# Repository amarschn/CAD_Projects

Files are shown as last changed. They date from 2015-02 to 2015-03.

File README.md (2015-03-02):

# CAD_Projects

MRSD Project:
=============

In this project my team and I (4 members) are focused on creating a modular robotic platform. Modules have been broken out based on different functions, such as perception, locomotion, and brain. We use ROS for inter-module communication over ethernet.

For this modular platform we built a mobile robot for the first semester consisting of a perception module, locomotion module, and brain module. The perception module was a pan/tilt Kinect camera which could be used for line sensing and tele-operation. The locomotion module was a differential drive system using 2 DC motors and caster wheels for support. The brain module was an Intel-i3 computer running ROS and controlling all other modules, a 24V battery, and voltage converter.

More details can be found at:
https://sites.google.com/site/mrsdproject201415teamd/

Semester 1:
-----------

Below is a picture of the full assembly of the last semester's robot.
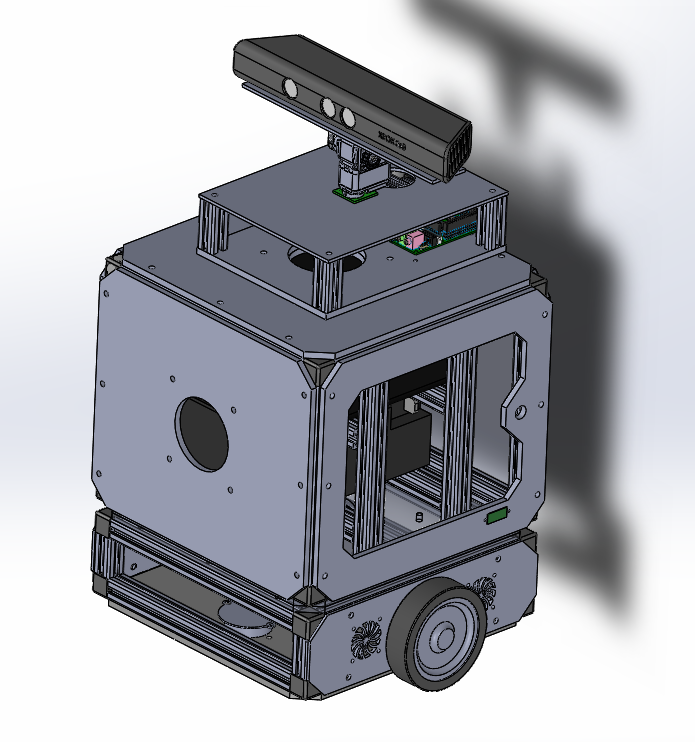
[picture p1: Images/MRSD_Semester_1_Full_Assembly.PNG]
Robot Assembly


The design of this robot was rather rushed, and so I focused on minimal build time and easy access to internal components (which proved smart, as the team and I had to dis-assemble and re-assemble the robot many times during testing in order to get access to electronic components). This was my first heavy use of Solidworks, as at Qualcomm I used Pro-Engineer/Creo. Overall I found the 2 programs more similar than different so the learning curve was not too bad.

At Qualcomm I used a top-down design method when constructing assemblies, which has it's pros and cons, but this time around I tried a different tack. I used a text file ("globals.txt") that contained global variables such as module height, width, etc.. I then imported the "global" variables into given Solidworks parts to access the variables I needed. This allowed me to quickly tweak robot physical parameters and have the changes affect all parts at once.

Here is the actual robot once constructed:
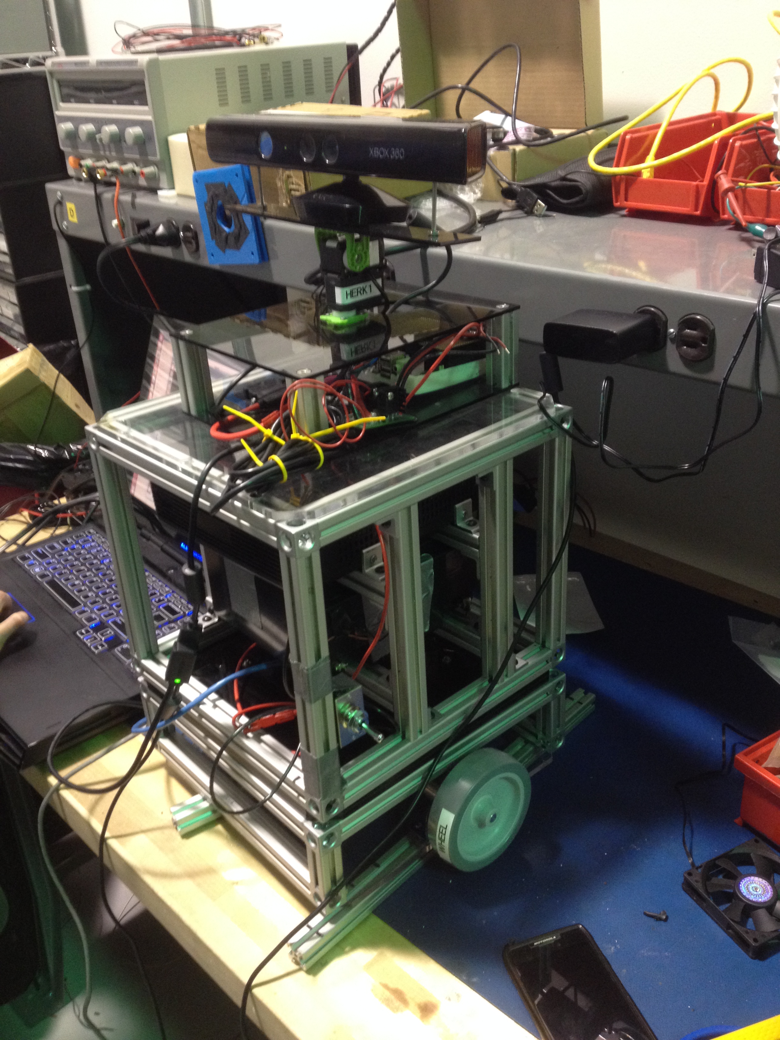
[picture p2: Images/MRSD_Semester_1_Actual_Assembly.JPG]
Actual Robot Assembly


This was my first mobile robot design, and I learned a lot from it. The large unfilled holes you see are for an inter-module connector. We were not able to finish a satisfactory inter-module connector in time for the end of last semester, and so the holes were used for ethernet and power wires.

I used laser-cut acrylic and aluminum extrusion as the mechanical structure of the robot. Due to time constraints I wanted something that was cheap, durable, and cost very little machining time. I had access to Makerbot 3D printers, which while useful for small parts are not useful for large, detailed, or load-bearing components.

Once all modules were assembled, the motor power was not always enough to get the robot moving over the rough pavement we demo'd on. The wear and tear of driving on rough pavement eventually caused a gear tooth in one of the motors' gearheads to crack (right before a demo of course), forcing us to change out the locomotion module for an existing mobile base for the final demo.

Semester 2 (now):
-----------------

This semester I have gone back to basics. I am re-designing the robot from the ground up, first focusing on the inter-module connection, as it is in many ways the most unique aspect of the robot. I came up with many different design possibilities, but eventually settled on a magnetic inter-module connector. Magnets offer many advantages, as the connection mechanical strength can be scaled to a point with larger magnets, and the disengagement between modules is linear. By this I mean that no special actions are required by the user to disengage a module other than pulling it. Additionally, by placing the magnets in certain pole orientations you can prevent the user from connecting 2 modules in an incorrect way.

This [paper](http://cba.mit.edu/docs/theses/10.06.knaian.pdf) considers many of the connector types I toyed with before settling on magnets. Ideally I would be able to prototype more of them, but there is not enough time before the end of the semester to fully explore all connector possibilities.

For the electrical connection I am using pogo pins, which are used to transmit power and data over 16 pins. I have used pogo pins before, and I think they are a no-brainer for applications such as this.

I am also using dowel pins as guide rods, which ensure an accurate pogo connection.

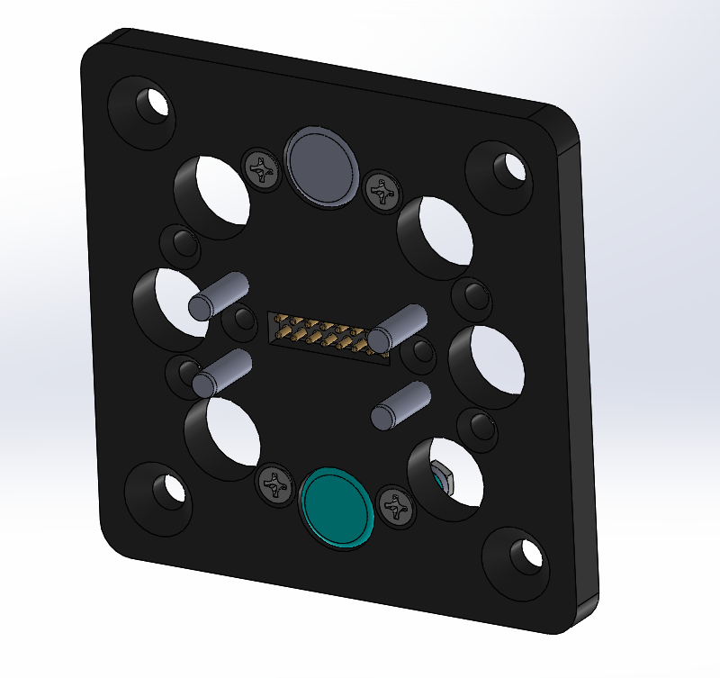
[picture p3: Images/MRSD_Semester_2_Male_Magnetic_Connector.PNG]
Male Magnetic Connector


This is the male connector, which as you can see is not using all of the magnet placement holes. This is because there was not enough room in the motor module for mounting all of them (the aluminum extrusion supports got in the way). This design is in a state of change however, and I am planning on using a different magnet placement grid to allow for more magnets.

The first module we have tested this magnetic connector with is a "motor module". This is a new module, one step lower than a locomotion module. The plan is to have motor modules that can be swapped out of a locomotion module, these different motor modules can have different kinds of motors as well as different wheel attachments. Once connected each motor module will communicate these details to the brain, which will dynamically update the robot's model. Below you can see the current CAD model for the motor module.

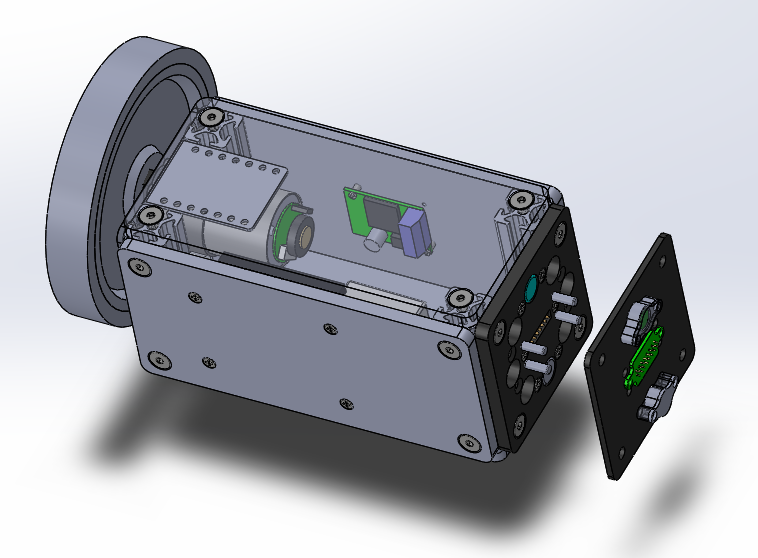
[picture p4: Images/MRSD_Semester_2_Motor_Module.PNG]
Motor Module


We have now built 2 of these, and they work pretty well! The magnetic connector works and is relatively sturdy. The next steps are to rebuild a locomotion base which will accept motor modules of this size, and to add the magnetic connector to appropriate faces of the brain module. We also will be building sensor modules using the same form factor as the motor module. So say the locomotion module had 4 different module connectors, you could swap out different motors and sensors quickly and easily and have an entirely new kind of robot! I am pretty excited about it and think by the end of the semester we will have a very cool re-configurable robot.

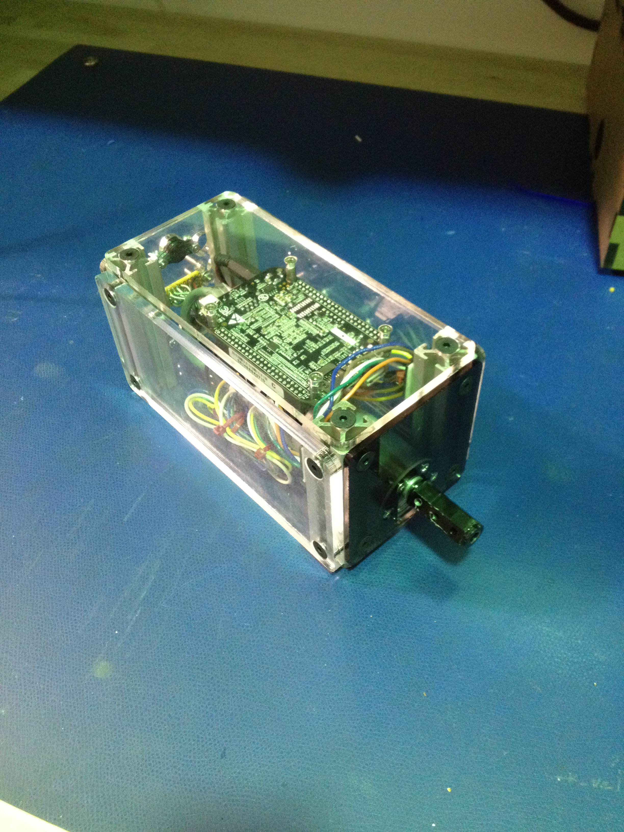
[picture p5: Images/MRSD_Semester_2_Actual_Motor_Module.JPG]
Actual Motor Module

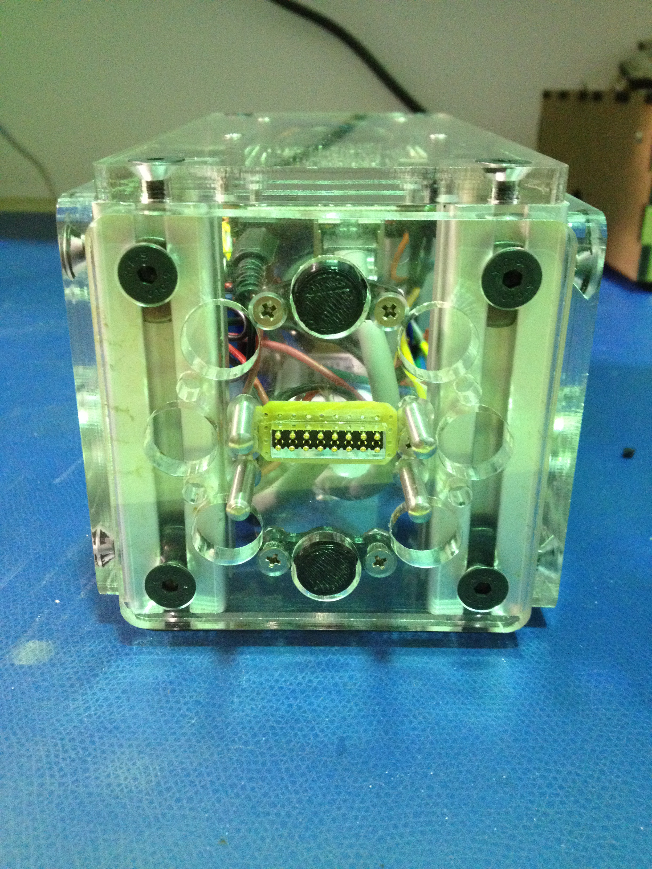
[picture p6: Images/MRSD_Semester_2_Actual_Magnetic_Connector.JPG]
Motor Module Connector


For the locomotion module, the plan is to have 4 module slots open to motor or sensor modules with the same form factor as the motor module seen above. I am trying to create a more visually pleasing aesthetic as compared to last semester. Below is one of the concepts for the module:

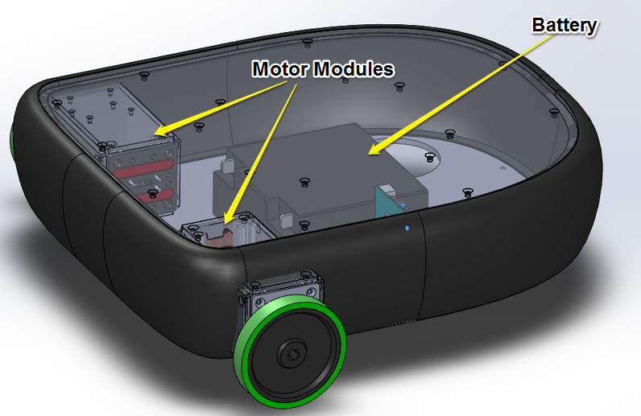
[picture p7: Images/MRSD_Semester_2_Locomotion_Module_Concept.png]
Locomotion Module Concept


By using laser cut acrylic or delrin on the top and bottom, and a thin 3D-printed ABS shell, the robot will be much more sleek as well as well within the team's limited budget.

Automated Durometer:
--------------------

The files for this project are located in a different repository, which can be found [here] (https://github.com/amarschn/Durometer_Assembly). The top-level assembly is called 'Durometer_Assembly' and can be downloaded in STP format if necessary.

This was a brief project I worked on over Christmas break. The goal was to automate a durometer (device for measuring hardness of different materials, in this case different kinds of rubber) for a scientific devices manufacturer.

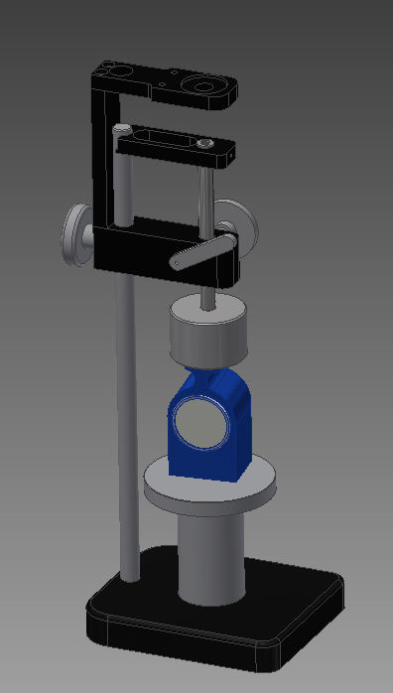
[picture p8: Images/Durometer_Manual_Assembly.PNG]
Basic Durometer


I did this project in Autodesk Inventor, as I wanted to try it out to see what all of the fuss was about. Once again, being a parametric CAD program it wasn't too different from Solidworks or Pro-E. The usual sketch/extrude/repeat process was mostly the same. My other focus was off-the-shelf material, as I did not have access to any kind of fabrication facilities during the majority of the break and so had to work with whatever I could get. McMaster was (once again) a godsend for this project.

In automating the durometer, I decided to implement a stepper-motor/lead screw system for raising and lowering the durometer. Steppers are relatively cheap and combined with lead screws allow for very accurate motion control, and no power draw during inactivity.

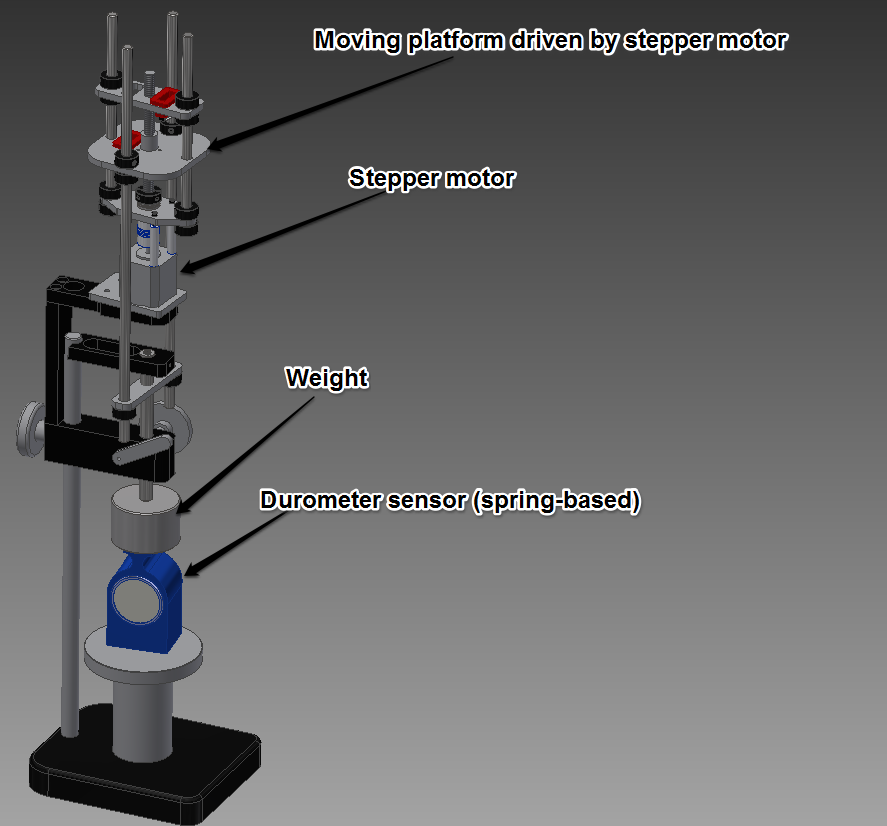
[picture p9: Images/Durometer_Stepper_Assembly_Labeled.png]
Automated Durometer

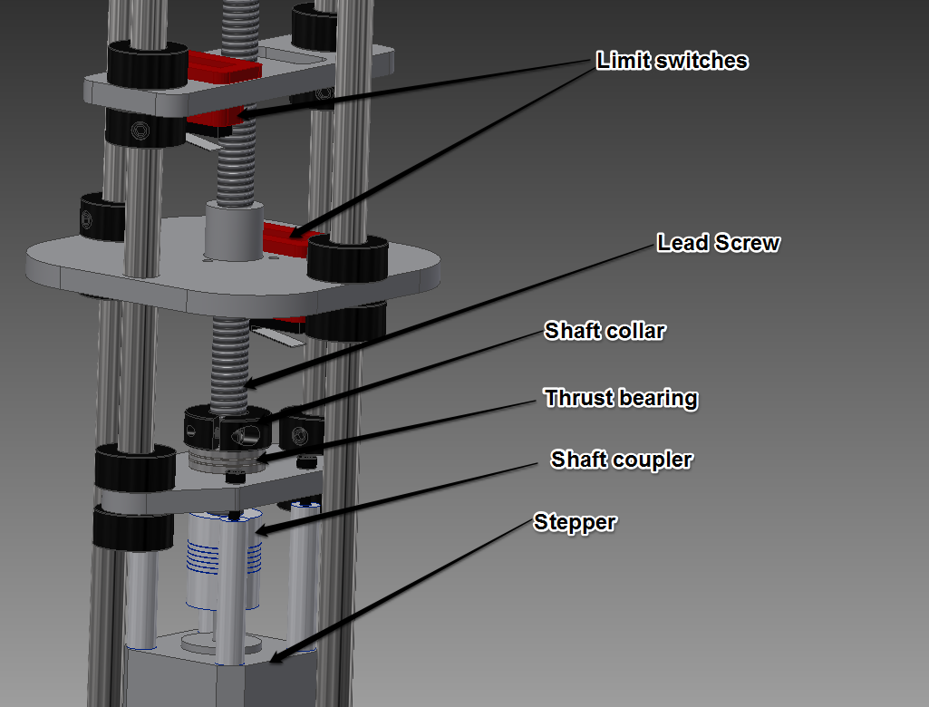
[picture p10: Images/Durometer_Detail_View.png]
Automated Durometer Detail


This project is currently on hiatus due to school taking up the majority of my time, but I was able to build a working prototype before the end of the break. Unfortunately I cannot find a video of it operating, but I will post that once I find it!

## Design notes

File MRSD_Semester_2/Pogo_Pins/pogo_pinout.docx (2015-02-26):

Female:

GND | GND | PWR | PWR | White w/orange stripe | White w/blue stripe | White w/green stripe | White w/brown stripe
GND | GND | PWR | PWR | Orange | Bue | Green | Brown

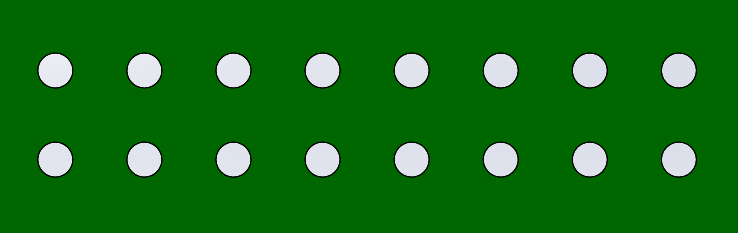
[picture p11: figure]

Male:

White w/brown stripe | White w/green stripe | White w/blue stripe | White w/orange stripe | PWR | PWR | GND | GND
Brown | Green | Blue | Orange | PWR | PWR | GND | GND

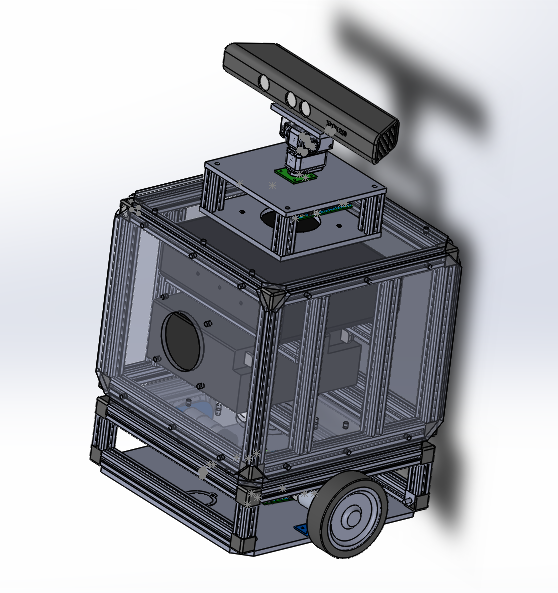
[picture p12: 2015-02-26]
MRSD_Semester_1/ILR4_img.png

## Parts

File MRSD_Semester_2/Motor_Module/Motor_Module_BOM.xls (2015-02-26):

ITEM NO. | PART NUMBER | DESCRIPTION | QTY.
1 | Motor |  | 1
2 | Motor Bracket |  | 1
3 | Motor Shaft Cover |  | 1
4 | Single Motor Driver |  | 1
5 | Rough BeagleBone Black |  | 1
6 | Motor_Module_Side_Pl ate |  | 1
7 | Motor_Module_Side_Pl ate |  | 1
8 | Motor_Module_Side_Pl ate |  | 1
9 | Motor_Module_Side_Pl ate |  | 1
10 | Motor_Module_Front_P late |  | 1
11 | Perm_Magnet_Male_Pl ate |  | 1
12 | 16pin_PCB |  | 1
13 | mill-max-823-22-016-10- 004101_P4XX-28-010- 00-090000 |  | 1
14 | mill-max-823-22-016-10- 004101_0963-0 |  | 16
15 | mill-max-823-22-016-10- 004101_0953-X |  | 16
16 | mill-max-823-22-016-10- 004101_0918-X |  | 16
17 | mill-max-823-22-016-10- 004101_6875-0-00-00- 75-XX-43-0C |  | 16
18 | Disc_Magnet_5862K65 |  | 8
19 | 93600A133 |  | 4
20 | T_Slot_Support |  | 4
21 | 91294A210 |  | 20
22 | 91771A059 |  | 2
23 | 94639A460 |  | 2
24 | 90730A001 |  | 2
25 | 91801A156 |  | 8
26 | 94868A164 |  | 4
27 | 90116A147 |  | 4
28 | Fastener_5537T454 |  | 16
29 | 91294A207 |  | 4
30 | 91801A154 |  | 6
31 | 90695A033 |  | 4
32 | Voltage Converter |  | 1

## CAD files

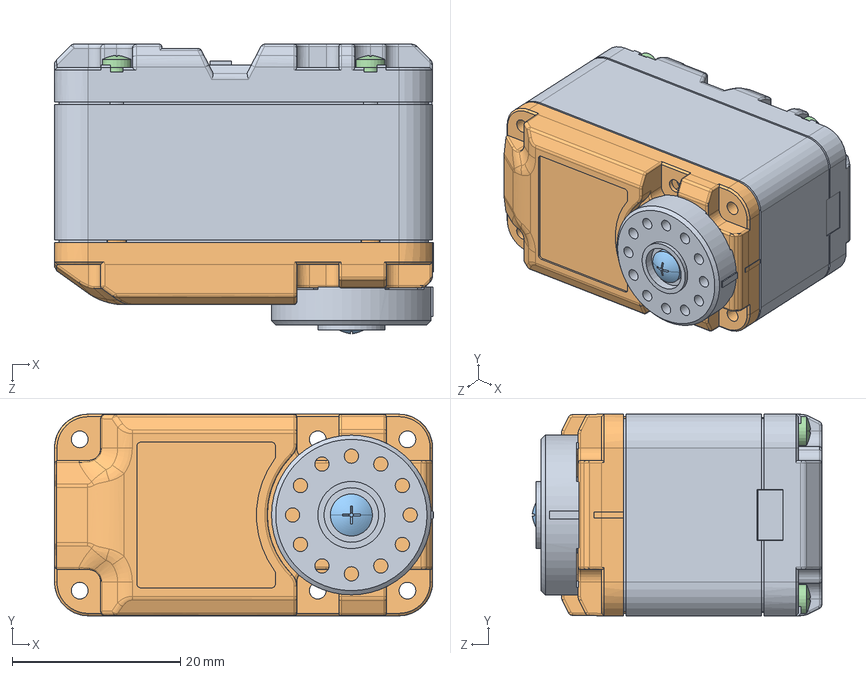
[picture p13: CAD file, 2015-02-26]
MRSD_Semester_1/SENSOR/herkulex.SLDASM
45.1 x 24.0 x 34.5 mm
Document
(#31287) TOP_191
(#129725) KSB1023A_M2_5X8Z
(#112458) KSB1023A_T2X25NI x 4

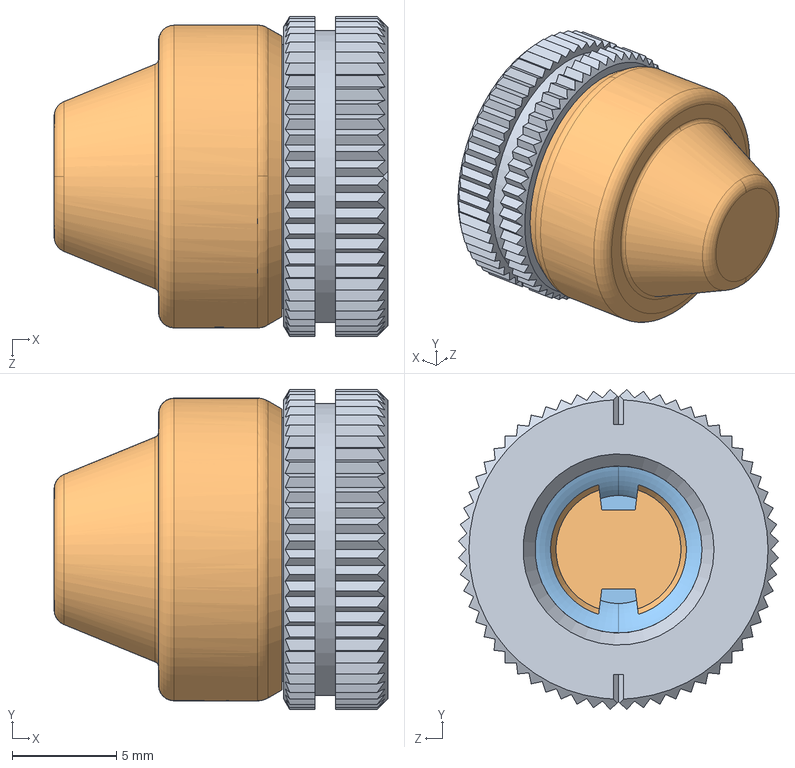
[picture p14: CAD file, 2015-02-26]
MRSD_Semester_2/Twist_Lock_Connectors/Southco-D8-336-100-300.SLDASM
16.0 x 15.3 x 15.3 mm
SW3dPS-D8-336-100-300_D8-336-101-300
SW3dPS-D8-336-100-300_D8-336-114-190-ASSY
SW3dPS-D8-336-100-300_D8-336-113-190

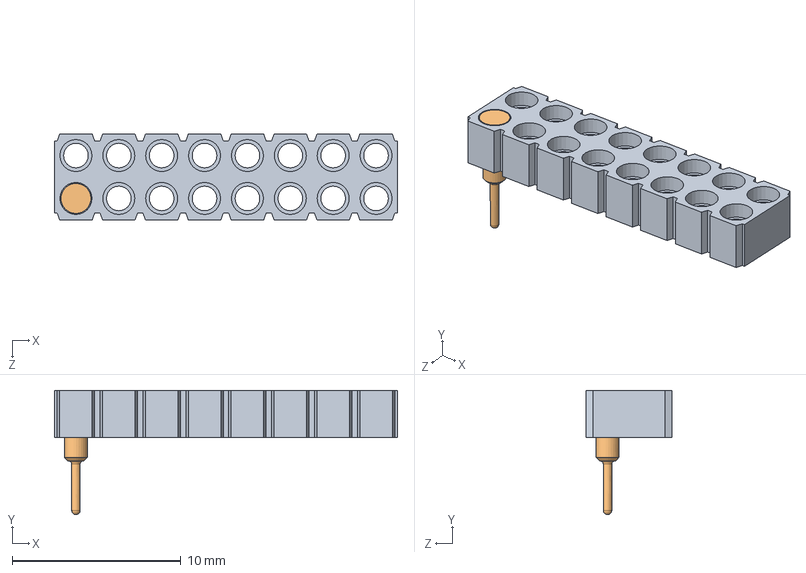
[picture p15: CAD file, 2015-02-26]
MRSD_Semester_2/Pogo_Pins/mill-max-419-10-216-00-001000/mill-max-419-10-216-00-001000.sldasm
20.3 x 7.37 x 5.08 mm
mill-max-419-10-216-00-001000_P4XX-21-010-00-000000
mill-max-419-10-216-00-001000_1942

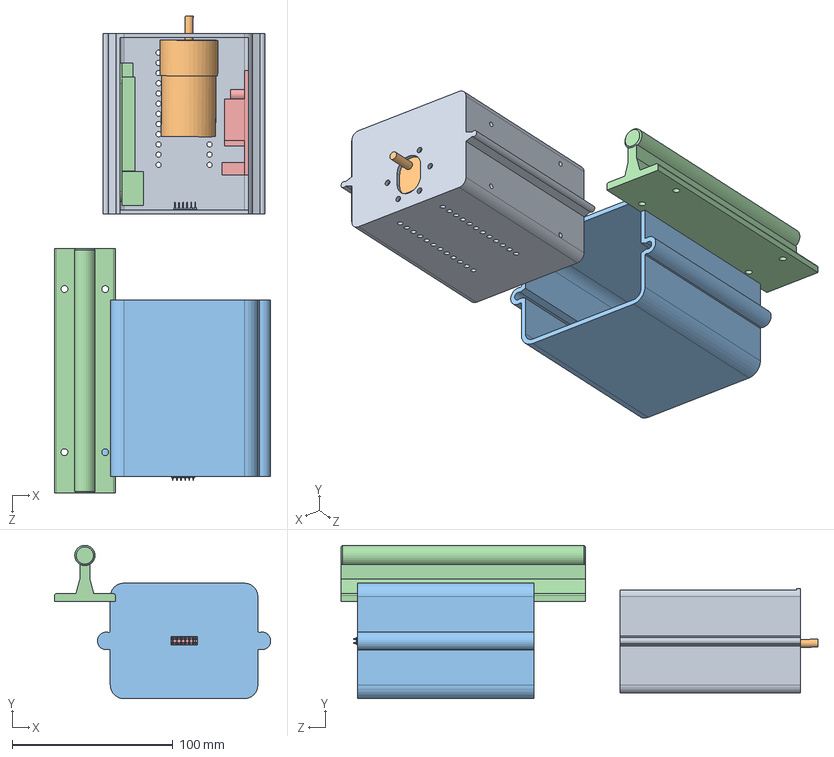
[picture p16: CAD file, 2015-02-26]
MRSD_Semester_2/Slide_Rail_Motor_Module/Slide_Rail_Assembly.SLDASM
134.8 x 95.5 x 297.1 mm
Slide_Rail_Motor_Housing
DC_Motor
Slide_Rail_Outer_Housing
Rough BeagleBone Black
mill-max-818-22-012-10-000101_P4XX-28-010-00-090000
mill-max-818-22-012-10-000101_0963-0 x 12
mill-max-818-22-012-10-000101_0954-0 x 12
mill-max-818-22-012-10-000101_0918-X x 12
mill-max-818-22-012-10-000101_6875-0-00-00-75-XX-43-0C x 12
mill-max-419-10-212-00-001000_P4XX-21-010-00-000000
mill-max-419-10-212-00-001000_1942 x 12
Slide_Rail_1049K110
Motor Driver

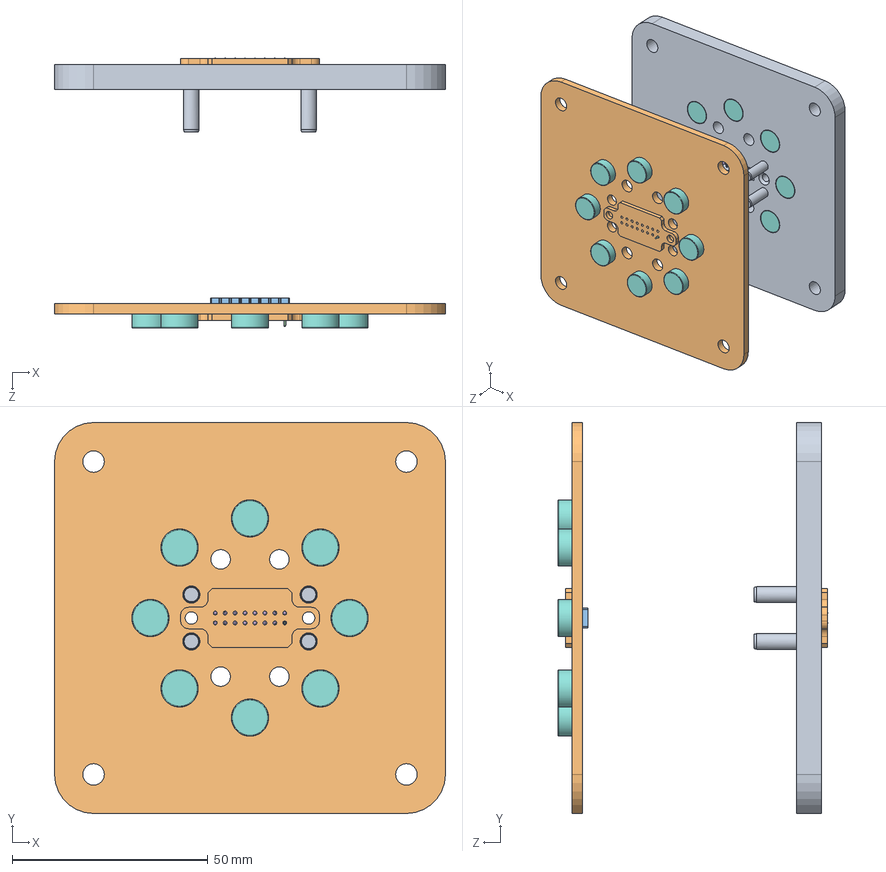
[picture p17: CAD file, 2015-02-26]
MRSD_Semester_2/Magnetic_Connectors/Perm_Magnet_Assembly.SLDASM
100.0 x 100.0 x 69.1 mm
Perm_Magnet_Male_Plate
16pin_PCB x 2
mill-max-823-22-016-10-004101_P4XX-28-010-00-090000
mill-max-823-22-016-10-004101_0963-0 x 16
mill-max-823-22-016-10-004101_0953-X x 16
mill-max-823-22-016-10-004101_0918-X x 16
mill-max-823-22-016-10-004101_6875-0-00-00-75-XX-43-0C x 16
Disc_Magnet_5862K65 x 16
Dowel_Pin_93600A133 x 4
Perm_Magnet_Female_Plate
mill-max-419-10-216-00-001000_P4XX-21-010-00-000000
mill-max-419-10-216-00-001000_1942

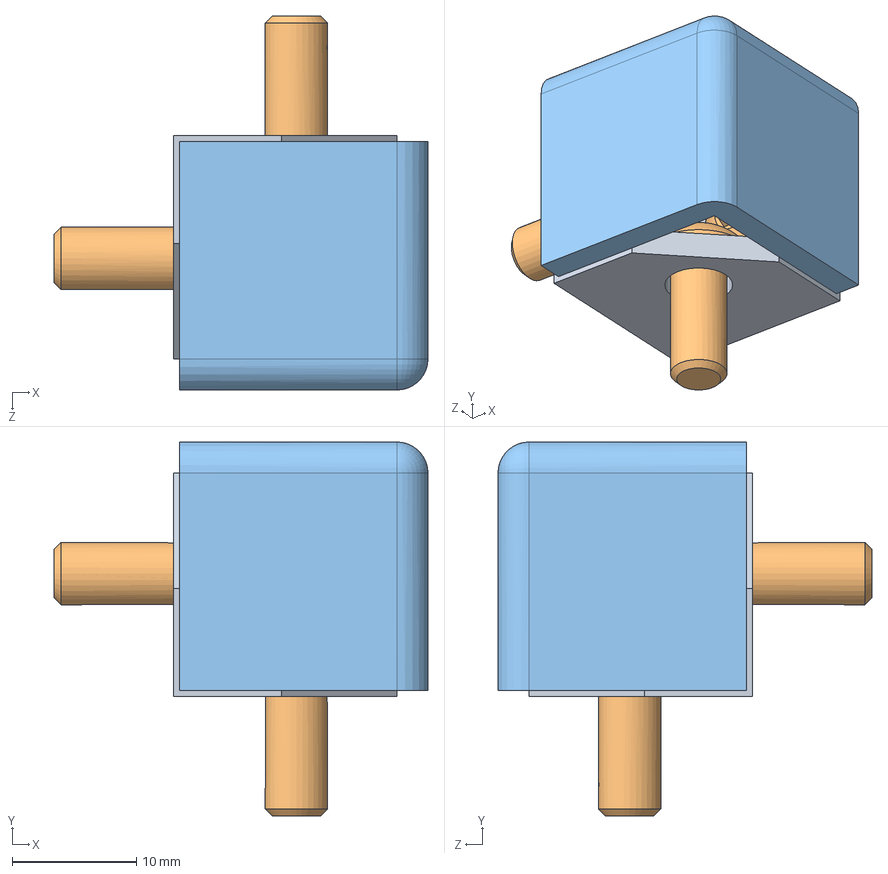
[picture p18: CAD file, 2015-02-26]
MRSD_Semester_1/BRAIN/corner_fastener.SLDASM
30.1 x 30.1 x 30.1 mm
corner_fastener_bracket
corner_fastener_screw x 3
corner_fastener_cover

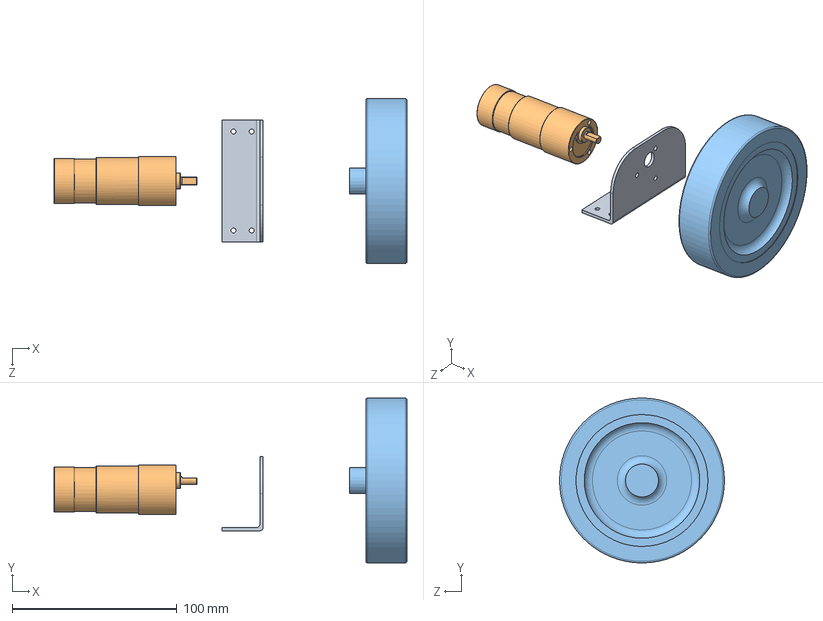
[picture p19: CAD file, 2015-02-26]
MRSD_Semester_1/LOCOMOTION/Devantech RD02 Drive System.SLDASM
214.1 x 99.9 x 100.0 mm
Devantech EMG30 Mounting Bracket
Devantech EMG30
Wheel

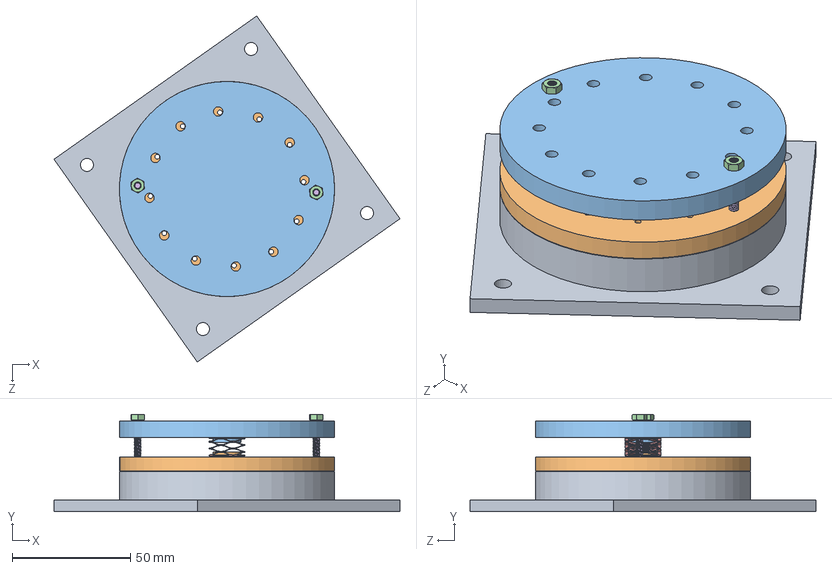
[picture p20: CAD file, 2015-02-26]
MRSD_Semester_1/CONNECTOR/bay con 12 mk2.SLDASM
146.3 x 41.1 x 146.3 mm
bayonet container 12
inner bayonet connector 12
bay container 12 bottom
m3 nut x 2
8mm length spring
M3 25MM x 2

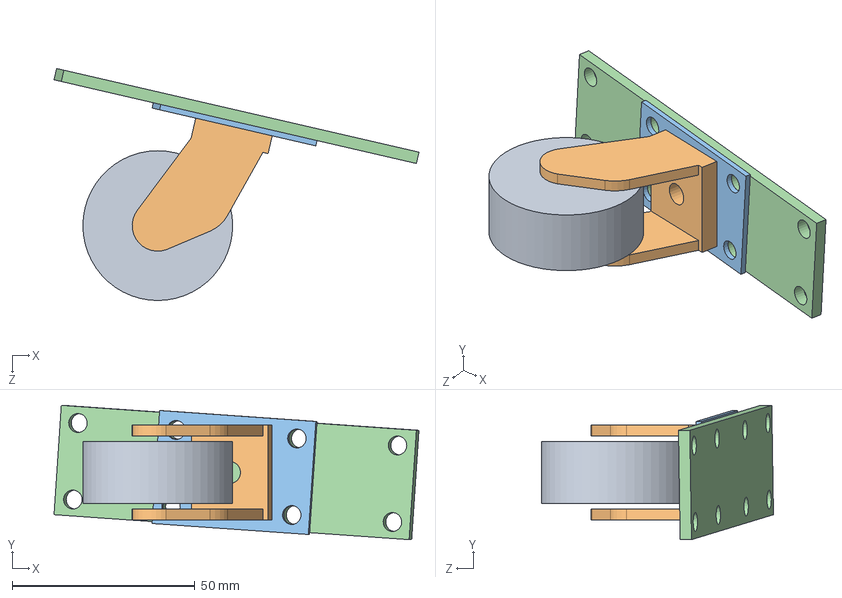
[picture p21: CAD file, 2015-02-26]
MRSD_Semester_1/LOCOMOTION/caster_wheel_assembly.SLDASM
99.9 x 36.8 x 63.5 mm
caster_wheel
caster_frame
caster_spin_plate
caster_mounting_plate

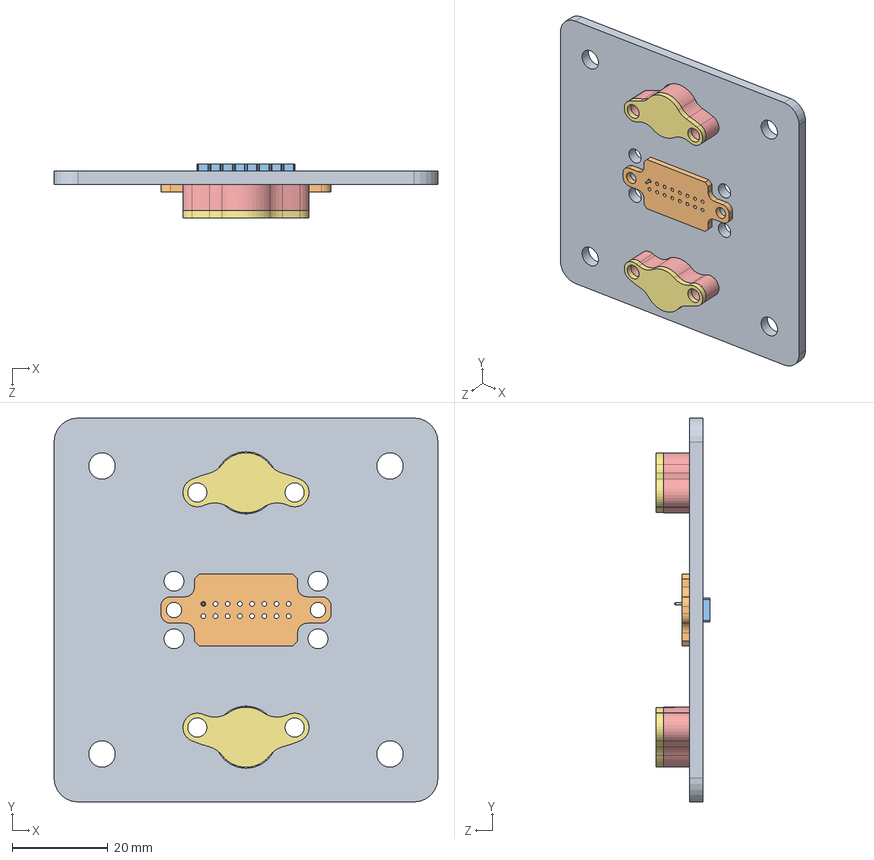
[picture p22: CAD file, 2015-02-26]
MRSD_Semester_2/Magnetic_Connectors/Female_Module_Connector_Assembly.SLDASM
80.0 x 80.0 x 11.2 mm
Perm_Magnet_Female_Plate
16pin_PCB
mill-max-419-10-216-00-001000_P4XX-21-010-00-000000
mill-max-419-10-216-00-001000_1942
Magnet_Containment_Vessel_Body x 2
Disc_Magnet_5862K65 x 2
Magnet_Containment_Vessel_Lid x 2

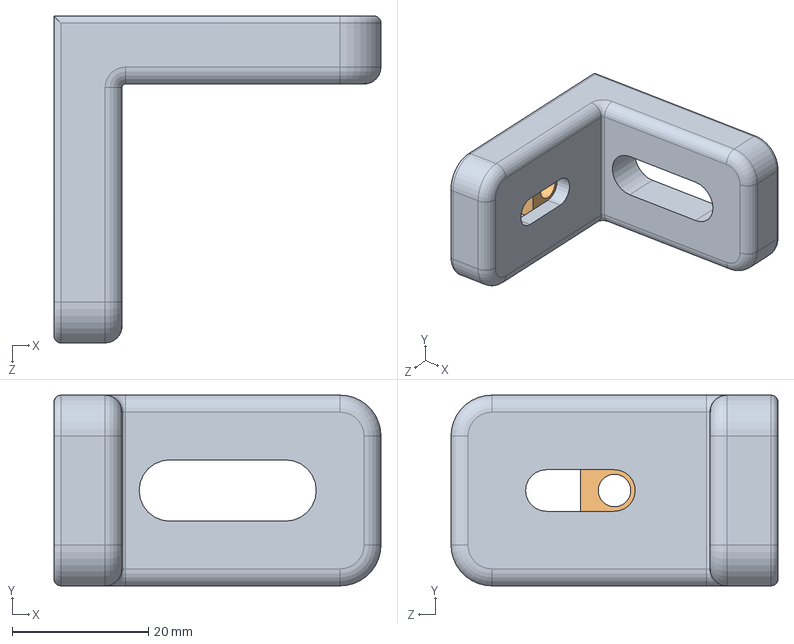
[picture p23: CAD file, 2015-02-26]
MRSD_Semester_1/BRAIN/t_slot_fastener.SLDASM
48.0 x 28.0 x 48.0 mm
t_slot_fastener_bracket
t_slot_fastener_slide

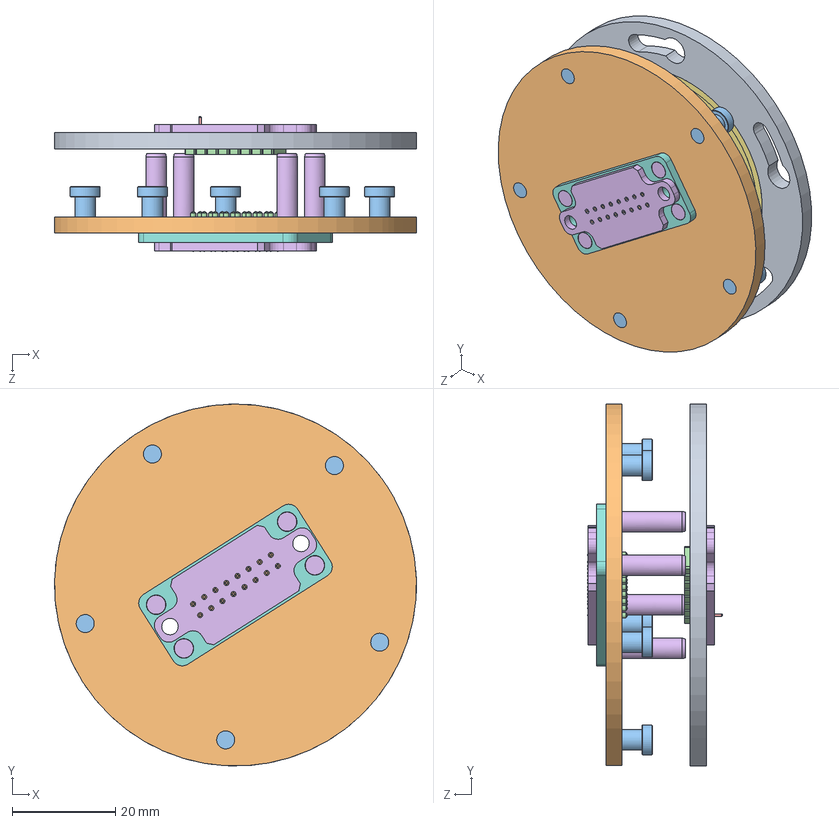
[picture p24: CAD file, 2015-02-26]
MRSD_Semester_2/Twist_Lock_Connectors/Star_Twist_Lock.SLDASM
70.0 x 70.0 x 26.2 mm
Star_Twist_Lock_Female_Plate
Star_Twist_Lock_Male_Plate
dowel_shelf_pin x 5
mill-max-419-10-216-00-001000_P4XX-21-010-00-000000
mill-max-419-10-216-00-001000_1942
Dowel_Pin_93600A133 x 4
Pogo_Fixture_Female_Front_Plate
Pogo_Fixture_Male_Front_Plate
mill-max-823-22-016-10-004101_P4XX-28-010-00-090000
mill-max-823-22-016-10-004101_0963-0 x 16
mill-max-823-22-016-10-004101_0953-X x 16
mill-max-823-22-016-10-004101_0918-X x 16
mill-max-823-22-016-10-004101_6875-0-00-00-75-XX-43-0C x 16
16pin_PCB x 2
Twist_Lock_Bearing

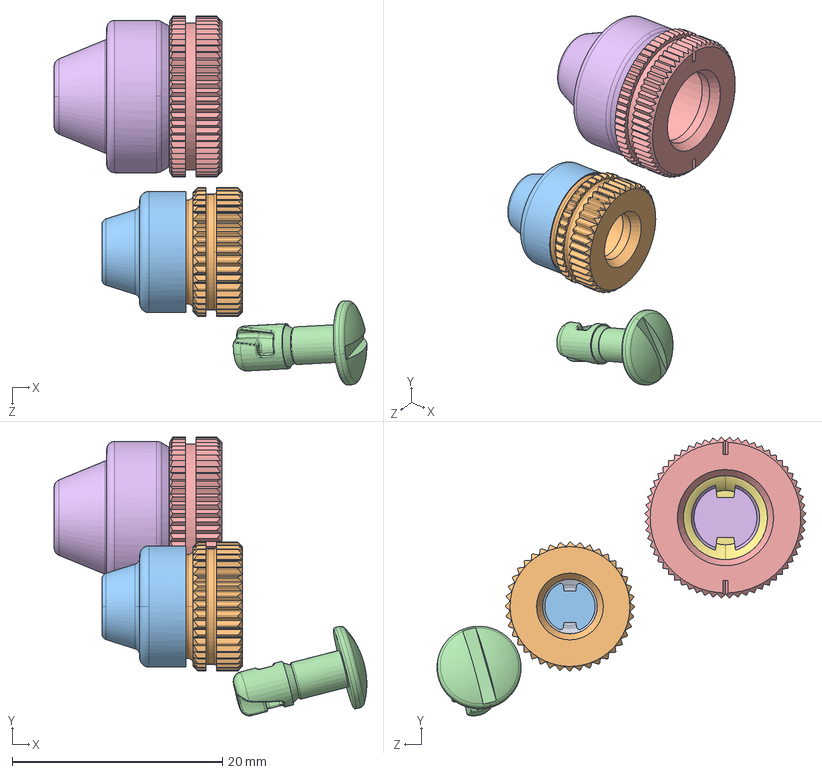
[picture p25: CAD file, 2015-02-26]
MRSD_Semester_2/Twist_Lock_Connectors/Test_Twist_Lock_Assembly.SLDASM
29.8 x 26.5 x 35.1 mm
SW3dPS-D8-334-100-300_TAB PLATE
SW3dPS-D8-334-100-300_D3_PANEX_Front_Mount_Insert_Body
SW3dPS-D8-334-100-300_D3_PANEX_Insert_Cup
Southco-D8-314-108-170
SW3dPS-D8-336-100-300_D8-336-101-300
SW3dPS-D8-336-100-300_D8-336-114-190-ASSY
SW3dPS-D8-336-100-300_D8-336-113-190

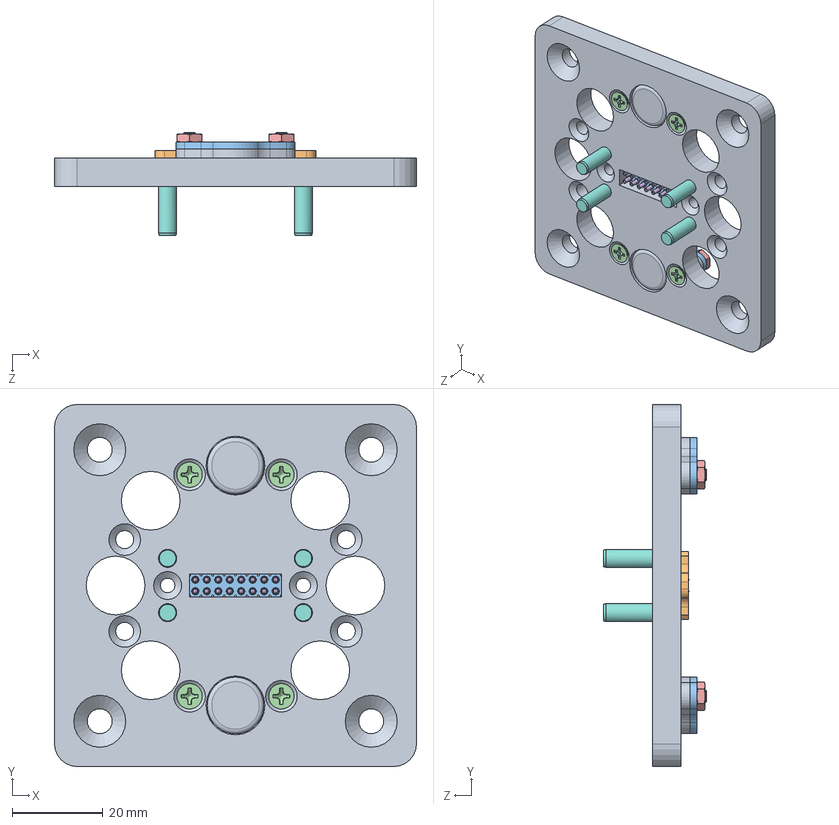
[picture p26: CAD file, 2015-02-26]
MRSD_Semester_2/Magnetic_Connectors/Male_Module_Connector_Assembly.SLDASM
80.0 x 80.0 x 22.9 mm
Perm_Magnet_Male_Plate
16pin_PCB
mill-max-823-22-016-10-004101_P4XX-28-010-00-090000
mill-max-823-22-016-10-004101_0963-0 x 16
mill-max-823-22-016-10-004101_0953-X x 16
mill-max-823-22-016-10-004101_0918-X x 16
mill-max-823-22-016-10-004101_6875-0-00-00-75-XX-43-0C x 16
Dowel_Pin_93600A133 x 4
Magnet_Containment_Vessel_Body x 2
Disc_Magnet_5862K65 x 2
Magnet_Containment_Vessel_Lid x 2
91801A158 x 4
90695A033 x 4

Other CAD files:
MRSD_Semester_2/Slide_Rail_Motor_Module/Locomotion_Base_Assembly.SLDASM
MRSD_Semester_2/Sketch_References/Perm_Magnet_Assembly_Reference.SLDPRT
MRSD_Semester_2/Magnetic_Connectors/Perm_Magnet_Assembly_Reference.SLDASM
MRSD_Semester_2/Pogo_Pins/16_pin_pogo_male_assembly.SLDASM
MRSD_Semester_1/ARM/gripper.stp
MRSD_Semester_1/ARM/uArm/gripper.stp
MRSD_Semester_1/BRAIN/5537T181.SLDPRT
MRSD_Semester_1/BRAIN/LED_voltage_display.SLDPRT
MRSD_Semester_1/BRAIN/anker_battery_form_factor.SLDPRT
MRSD_Semester_1/BRAIN/assembly_brain_1.SLDASM
MRSD_Semester_1/BRAIN/assembly_brain_1.SLDDRW
MRSD_Semester_1/BRAIN/brain_front_panel.DXF
MRSD_Semester_1/BRAIN/brain_front_panel.SLDPRT
MRSD_Semester_1/BRAIN/brain_side_panel.DXF
MRSD_Semester_1/BRAIN/brain_side_panel.SLDPRT
MRSD_Semester_1/BRAIN/brain_side_panel_vents.SLDPRT
MRSD_Semester_1/BRAIN/brain_top_panel.DXF
MRSD_Semester_1/BRAIN/brain_top_panel.SLDPRT
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

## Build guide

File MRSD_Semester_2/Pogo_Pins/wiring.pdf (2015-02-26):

Female:

GND | GND | PWR | PWR | White w/orange stripe | White w/green stripe | White w/blue stripe | White w/brown stripe
GND | GND | PWR | PWR | Orange | Bue | Green | Brown

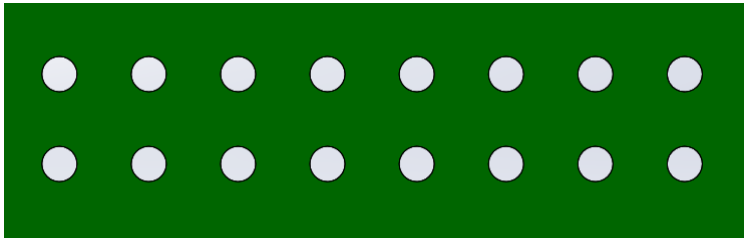
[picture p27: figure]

Male:

White w/brown stripe | White w/blue stripe | White w/green stripe | White w/orange stripe | PWR | PWR | GND | GND
Brown | Green | Bue | Orange | PWR | PWR | GND | GND

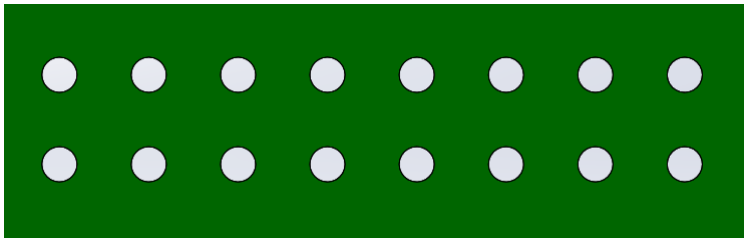
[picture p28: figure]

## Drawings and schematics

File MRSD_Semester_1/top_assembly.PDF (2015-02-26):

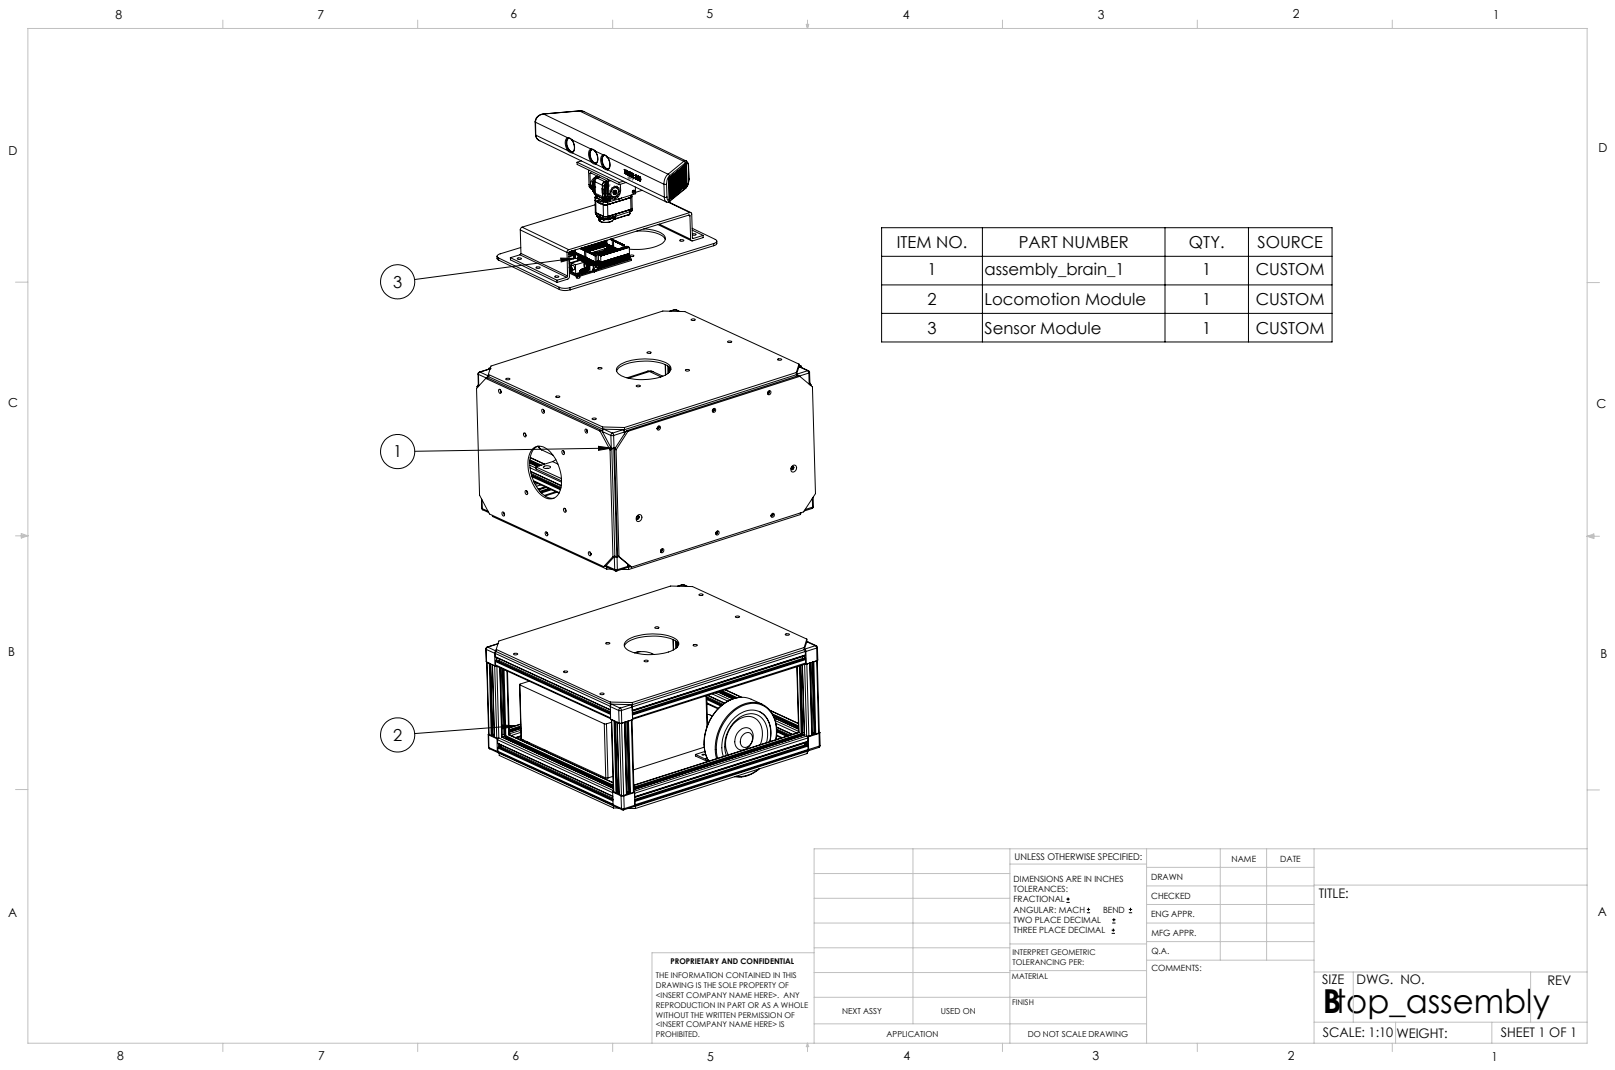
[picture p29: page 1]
NEXT ASSY; USED ON; ANGULAR: MACH; BEND; INTERPRET GEOMETRIC TOLERANCING PER:; ENG APPR.; MFG APPR.; DWG. NO.; REV; SCALE: 1:10 WEIGHT:; SHEET 1 OF 1

ITEM NO. | PART NUMBER | QTY. | SOURCE
1 | assembly_brain_1 | 1 | CUSTOM
2 | Locomotion Module | 1 | CUSTOM
3 | Sensor Module | 1 | CUSTOM

UNLESS OTHERWISE SPECIFIED:

DIMENSIONS ARE IN INCHES
TOLERANCES:
FRACTIONAL
TWO PLACE DECIMAL
THREE PLACE DECIMAL

PROPRIETARY AND CONFIDENTIAL
THE INFORMATION CONTAINED IN THIS
DRAWING IS THE SOLE PROPERTY OF
<INSERT COMPANY NAME HERE>. ANY
REPRODUCTION IN PART OR AS A WHOLE
WITHOUT THE WRITTEN PERMISSION OF
<INSERT COMPANY NAME HERE> IS
PROHIBITED.

DO NOT SCALE DRAWING

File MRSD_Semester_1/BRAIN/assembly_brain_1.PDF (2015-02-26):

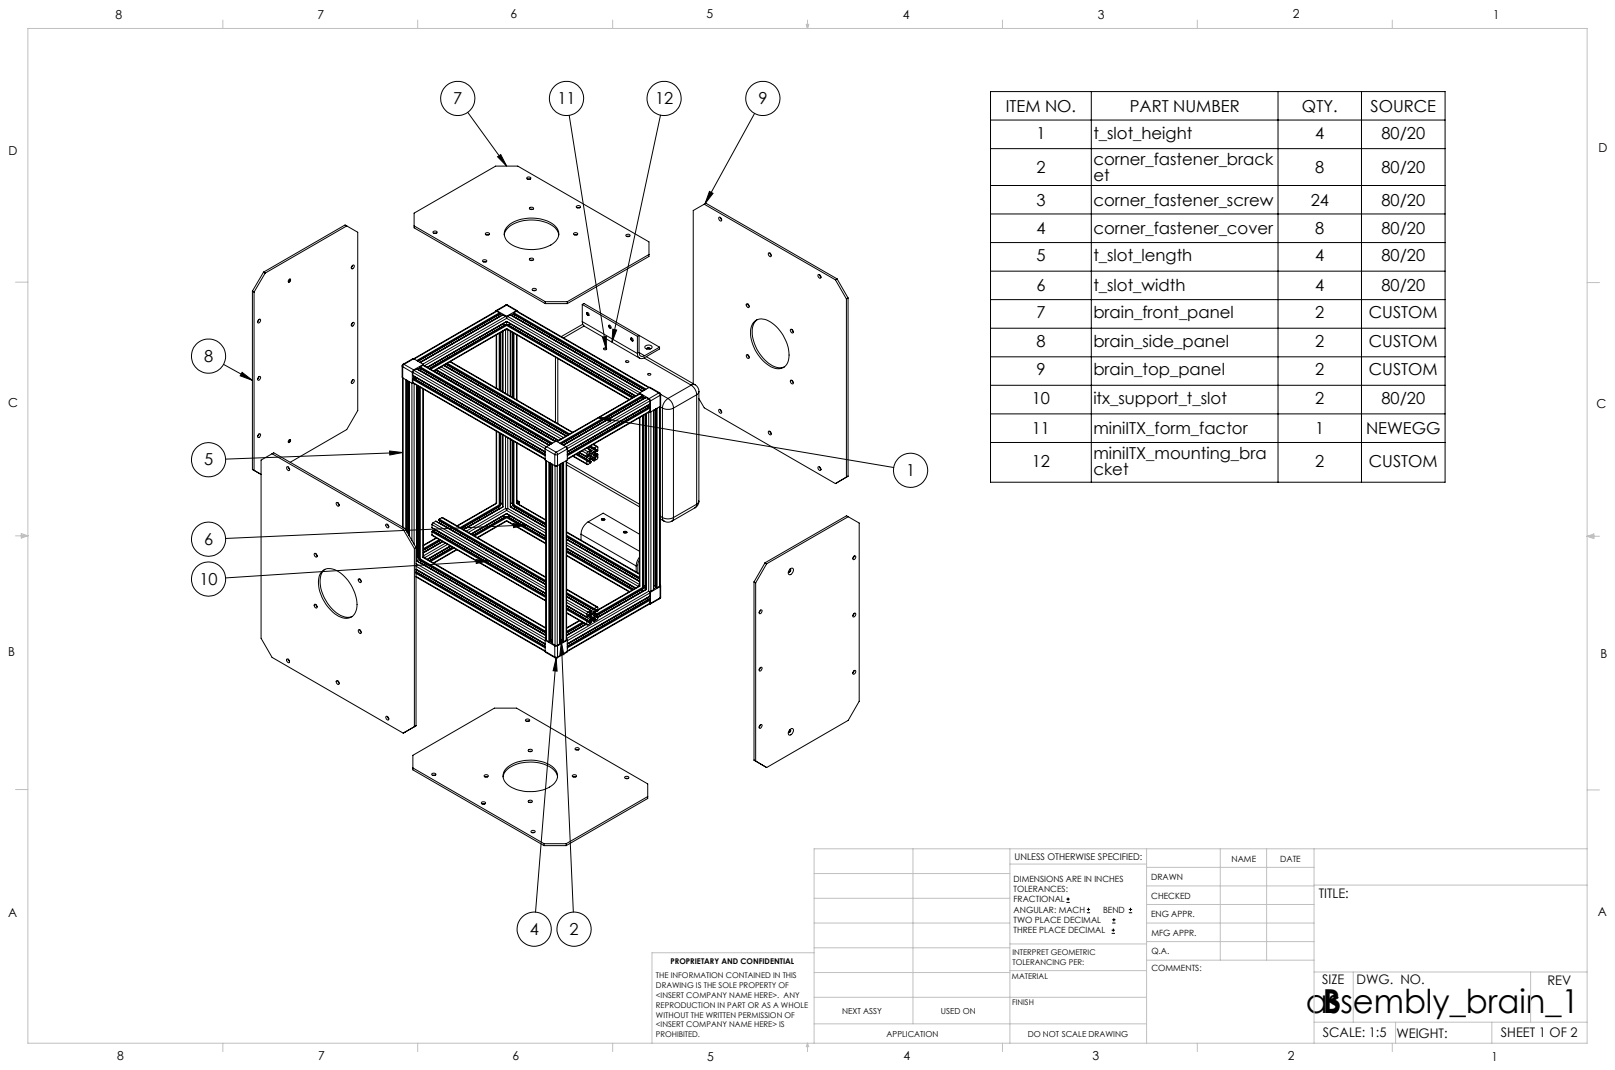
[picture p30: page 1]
NEXT ASSY; USED ON; ANGULAR: MACH; BEND; INTERPRET GEOMETRIC TOLERANCING PER:; ENG APPR.; MFG APPR.; DWG. NO.; REV; SCALE: 1:5 WEIGHT:; SHEET 1 OF 2

ITEM NO. | PART NUMBER | QTY. | SOURCE
1 | t_slot_height | 4 | 80/20
2 | corner_fastener_brack et | 8 | 80/20
3 | corner_fastener_screw | 24 | 80/20
4 | corner_fastener_cover | 8 | 80/20
5 | t_slot_length | 4 | 80/20
6 | t_slot_width | 4 | 80/20
7 | brain_front_panel | 2 | CUSTOM
8 | brain_side_panel | 2 | CUSTOM
9 | brain_top_panel | 2 | CUSTOM
10 | itx_support_t_slot | 2 | 80/20
11 | miniITX_form_factor | 1 | NEWEGG
12 | miniITX_mounting_bra cket | 2 | CUSTOM

UNLESS OTHERWISE SPECIFIED:

DIMENSIONS ARE IN INCHES
TOLERANCES:
FRACTIONAL
TWO PLACE DECIMAL
THREE PLACE DECIMAL

PROPRIETARY AND CONFIDENTIAL
THE INFORMATION CONTAINED IN THIS
DRAWING IS THE SOLE PROPERTY OF
<INSERT COMPANY NAME HERE>. ANY
REPRODUCTION IN PART OR AS A WHOLE
WITHOUT THE WRITTEN PERMISSION OF
<INSERT COMPANY NAME HERE> IS
PROHIBITED.

DO NOT SCALE DRAWING

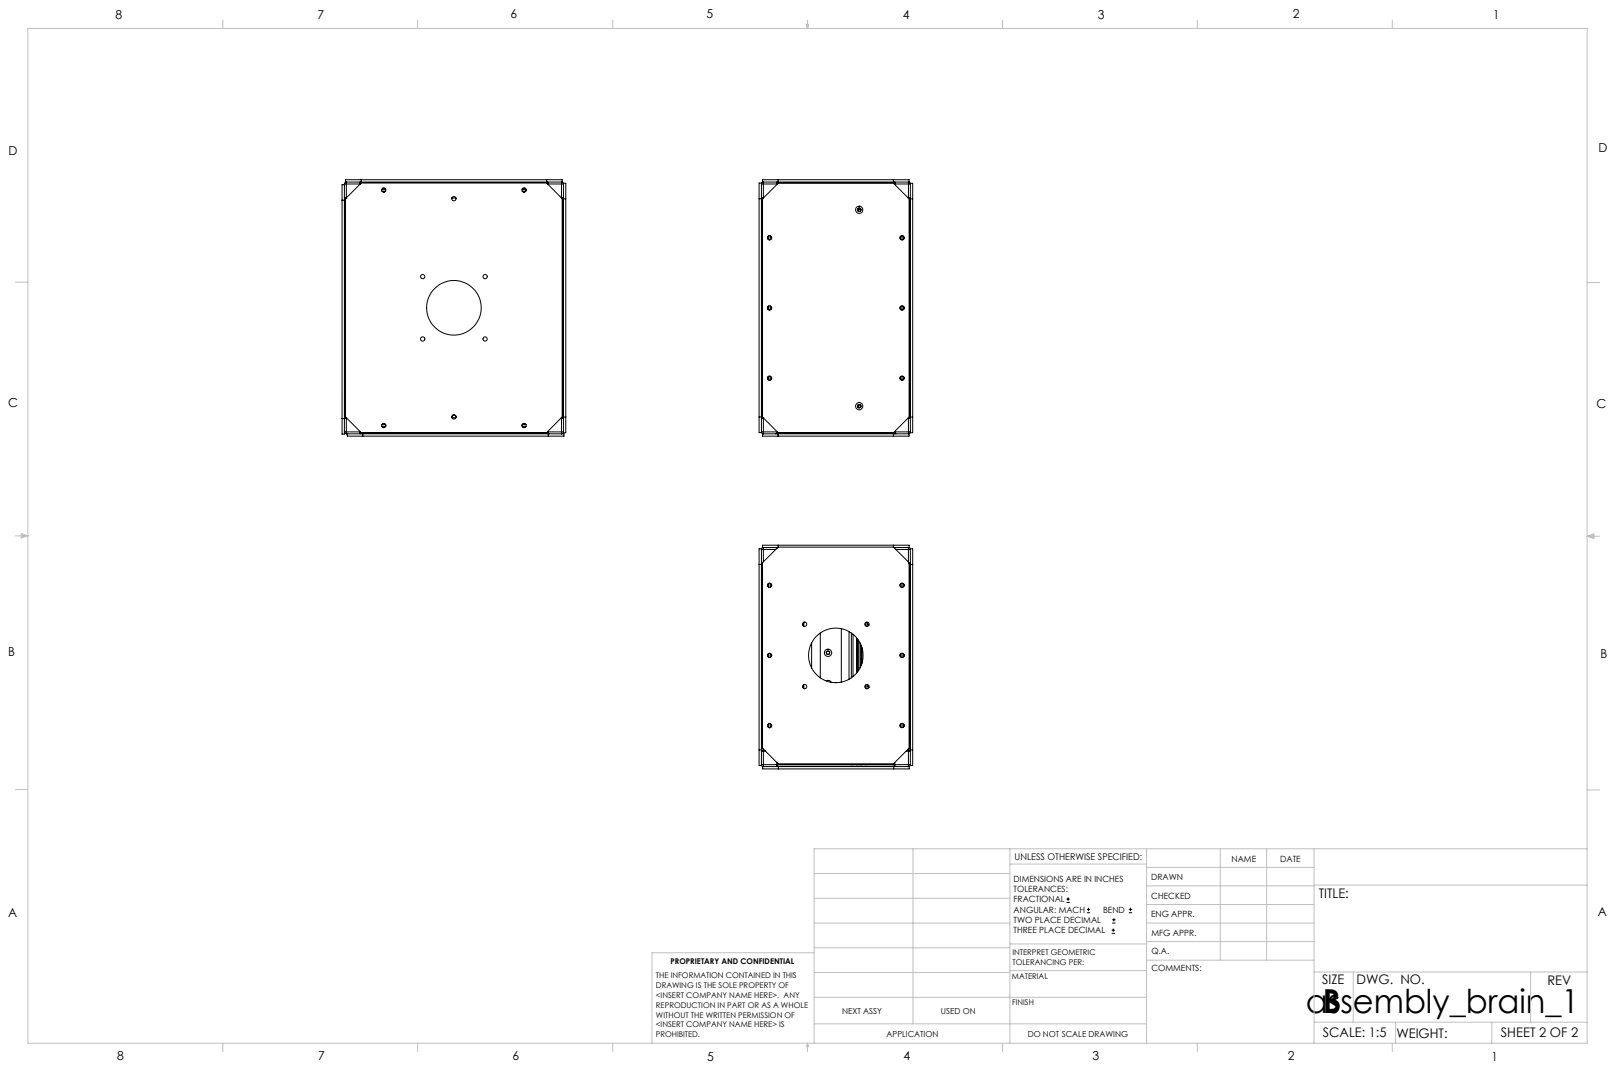
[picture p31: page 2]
NEXT ASSY; USED ON; ANGULAR: MACH; BEND; INTERPRET GEOMETRIC TOLERANCING PER:; ENG APPR.; MFG APPR.; DWG. NO.; REV; SCALE: 1:5 WEIGHT:; SHEET 2 OF 2

UNLESS OTHERWISE SPECIFIED:

DIMENSIONS ARE IN INCHES
TOLERANCES:
FRACTIONAL
TWO PLACE DECIMAL
THREE PLACE DECIMAL

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

DO NOT SCALE DRAWING

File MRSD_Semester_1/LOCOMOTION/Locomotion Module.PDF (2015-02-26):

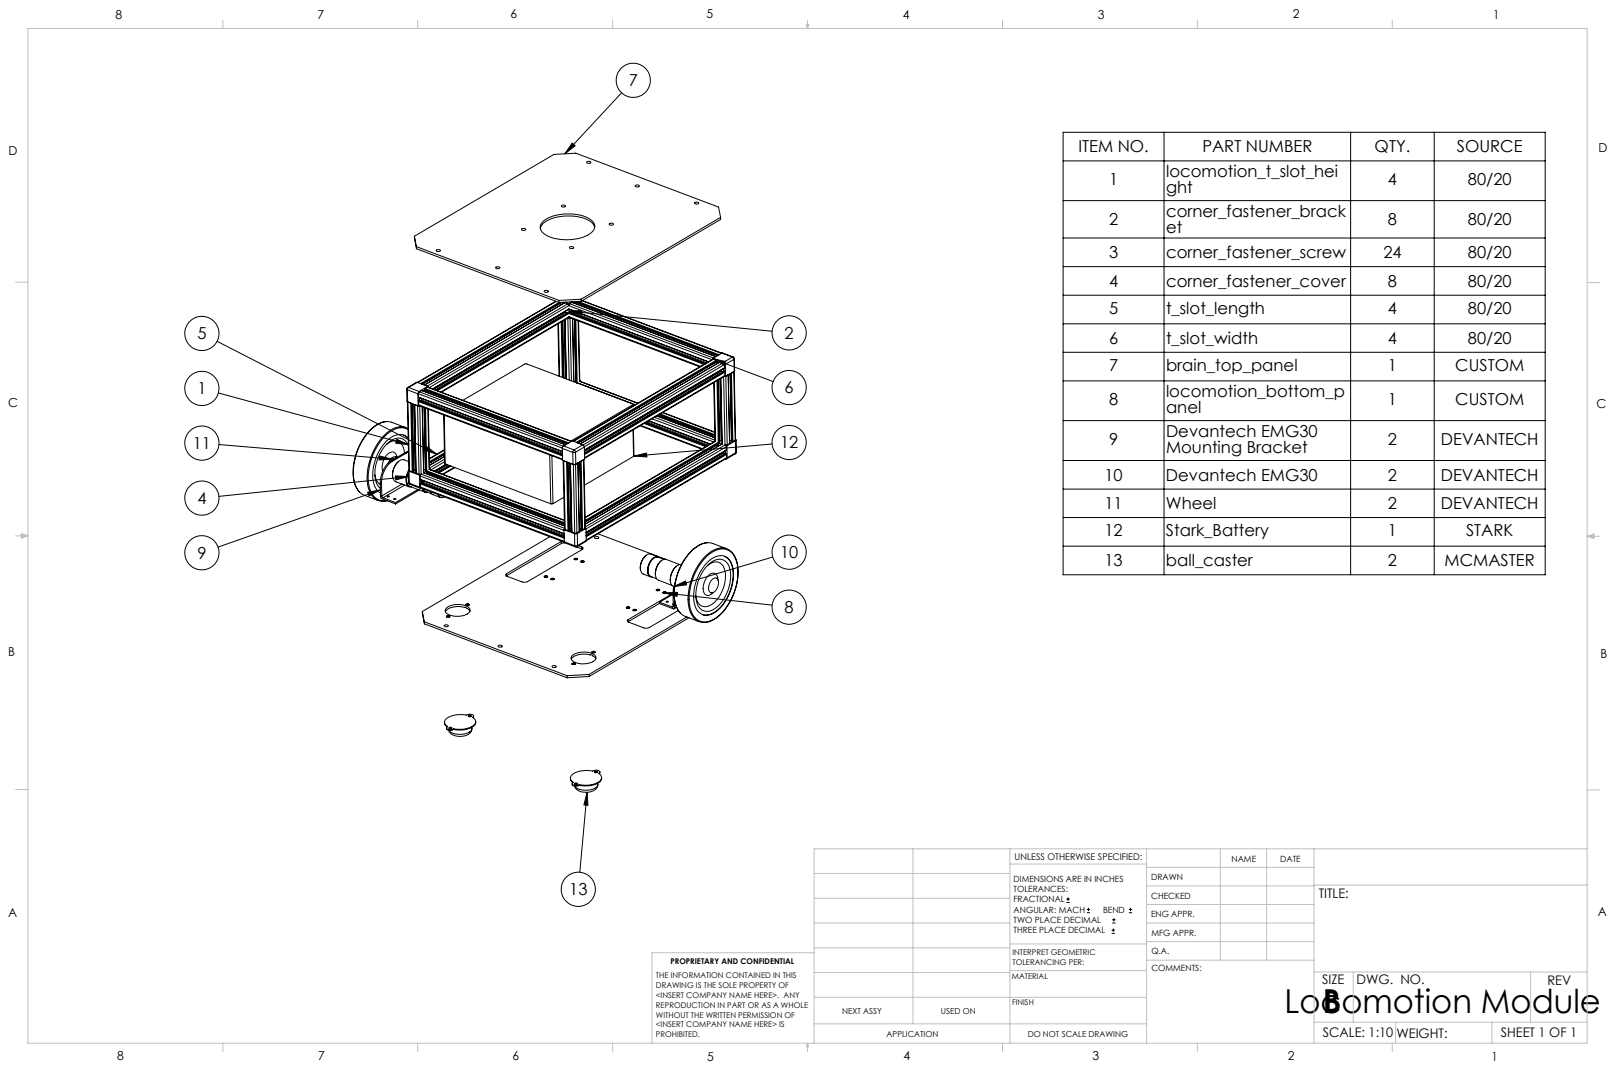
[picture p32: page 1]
NEXT ASSY; USED ON; ANGULAR: MACH; BEND; INTERPRET GEOMETRIC TOLERANCING PER:; ENG APPR.; MFG APPR.; DWG. NO.; REV; SCALE: 1:10 WEIGHT:; SHEET 1 OF 1; Locomotion Module

ITEM NO. | PART NUMBER | QTY. | SOURCE
1 | locomotion_t_slot_hei ght | 4 | 80/20
2 | corner_fastener_brack et | 8 | 80/20
3 | corner_fastener_screw | 24 | 80/20
4 | corner_fastener_cover | 8 | 80/20
5 | t_slot_length | 4 | 80/20
6 | t_slot_width | 4 | 80/20
7 | brain_top_panel | 1 | CUSTOM
8 | locomotion_bottom_p anel | 1 | CUSTOM
9 | Devantech EMG30 Mounting Bracket | 2 | DEVANTECH

10 | Devantech EMG30 | 2 | DEVANTECH
11 | Wheel | 2 | DEVANTECH
12 | Stark_Battery | 1 | STARK
13 | ball_caster | 2 | MCMASTER

UNLESS OTHERWISE SPECIFIED:

DIMENSIONS ARE IN INCHES
TOLERANCES:
FRACTIONAL
TWO PLACE DECIMAL
THREE PLACE DECIMAL

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

DO NOT SCALE DRAWING

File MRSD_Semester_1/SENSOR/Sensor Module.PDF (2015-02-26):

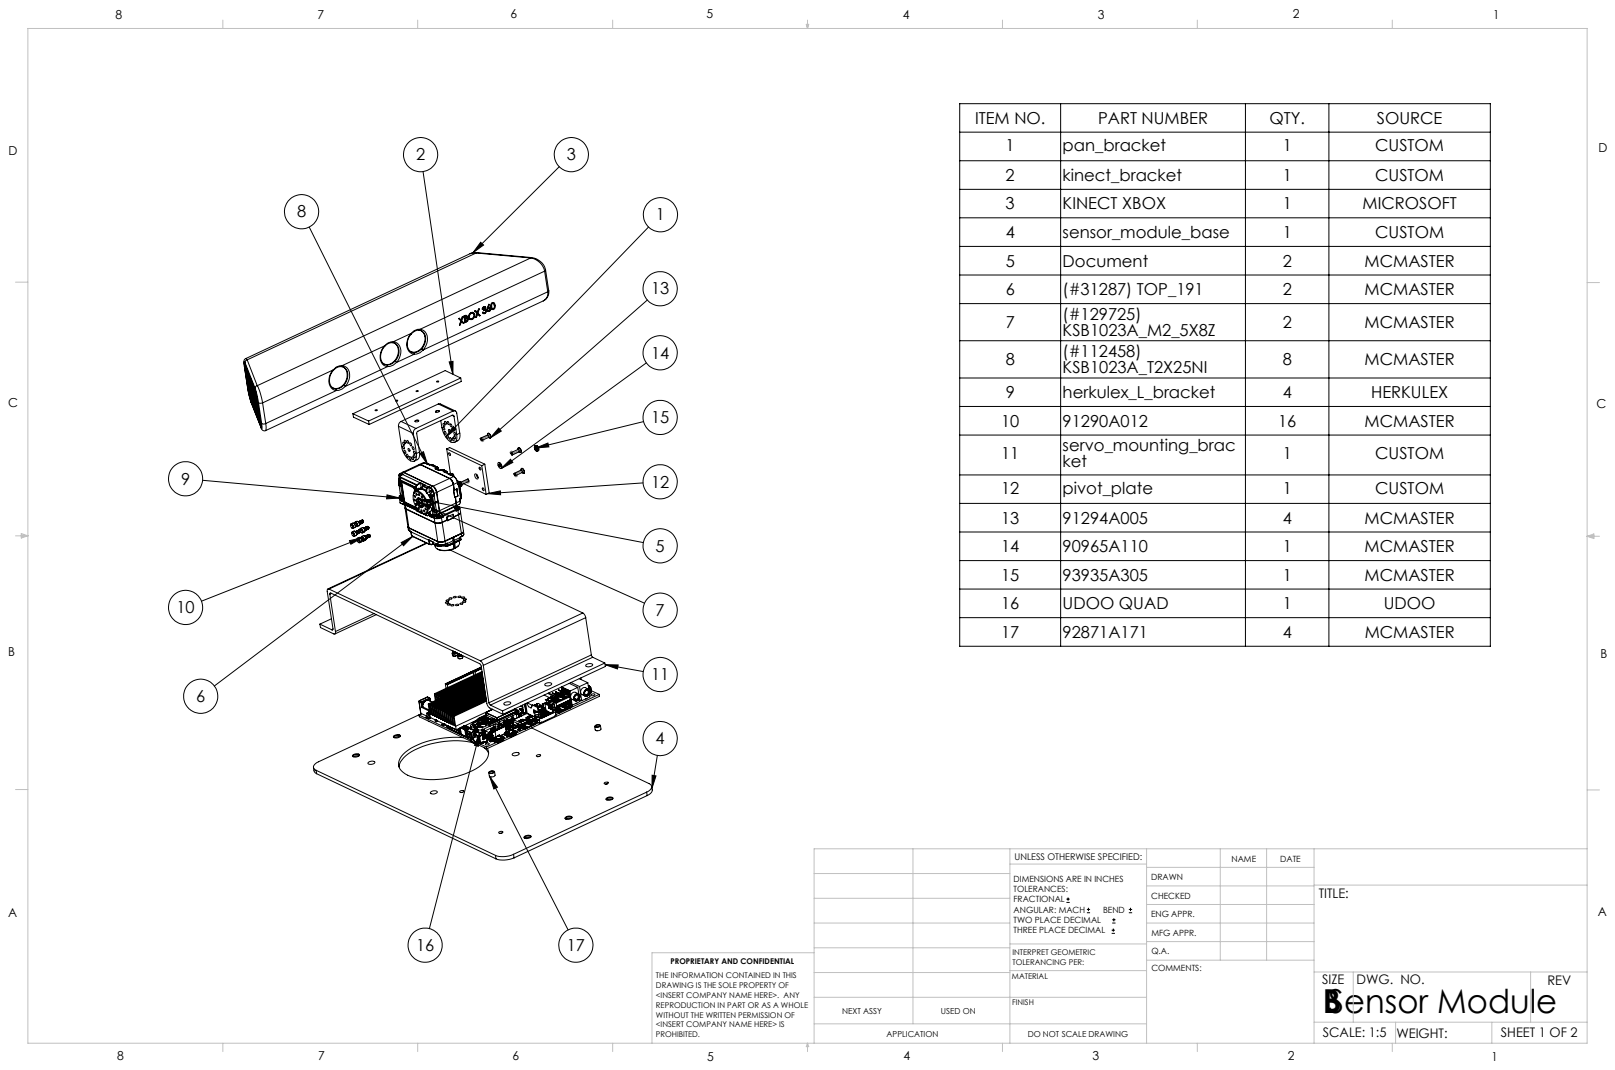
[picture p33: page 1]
NEXT ASSY; USED ON; ANGULAR: MACH; BEND; INTERPRET GEOMETRIC TOLERANCING PER:; ENG APPR.; MFG APPR.; DWG. NO.; REV; SCALE: 1:5 WEIGHT:; SHEET 1 OF 2; Sensor Module

ITEM NO. | PART NUMBER | QTY. | SOURCE
1 | pan_bracket | 1 | CUSTOM
2 | kinect_bracket | 1 | CUSTOM
3 | KINECT XBOX | 1 | MICROSOFT
4 | sensor_module_base | 1 | CUSTOM
5 | Document | 2 | MCMASTER
6 | (#31287) TOP_191 | 2 | MCMASTER
7 | (#129725) KSB1023A_M2_5X8Z | 2 | MCMASTER
8 | (#112458) KSB1023A_T2X25NI | 8 | MCMASTER
9 | herkulex_L_bracket | 4 | HERKULEX
10 | 91290A012 | 16 | MCMASTER
11 | servo_mounting_brac ket | 1 | CUSTOM
12 | pivot_plate | 1 | CUSTOM
13 | 91294A005 | 4 | MCMASTER
14 | 90965A110 | 1 | MCMASTER
15 | 93935A305 | 1 | MCMASTER
16 | UDOO QUAD | 1 | UDOO
17 | 92871A171 | 4 | MCMASTER

UNLESS OTHERWISE SPECIFIED:

DIMENSIONS ARE IN INCHES
TOLERANCES:
FRACTIONAL
TWO PLACE DECIMAL
THREE PLACE DECIMAL

PROPRIETARY AND CONFIDENTIAL
THE INFORMATION CONTAINED IN THIS
DRAWING IS THE SOLE PROPERTY OF
<INSERT COMPANY NAME HERE>. ANY
REPRODUCTION IN PART OR AS A WHOLE
WITHOUT THE WRITTEN PERMISSION OF
<INSERT COMPANY NAME HERE> IS
PROHIBITED.

DO NOT SCALE DRAWING

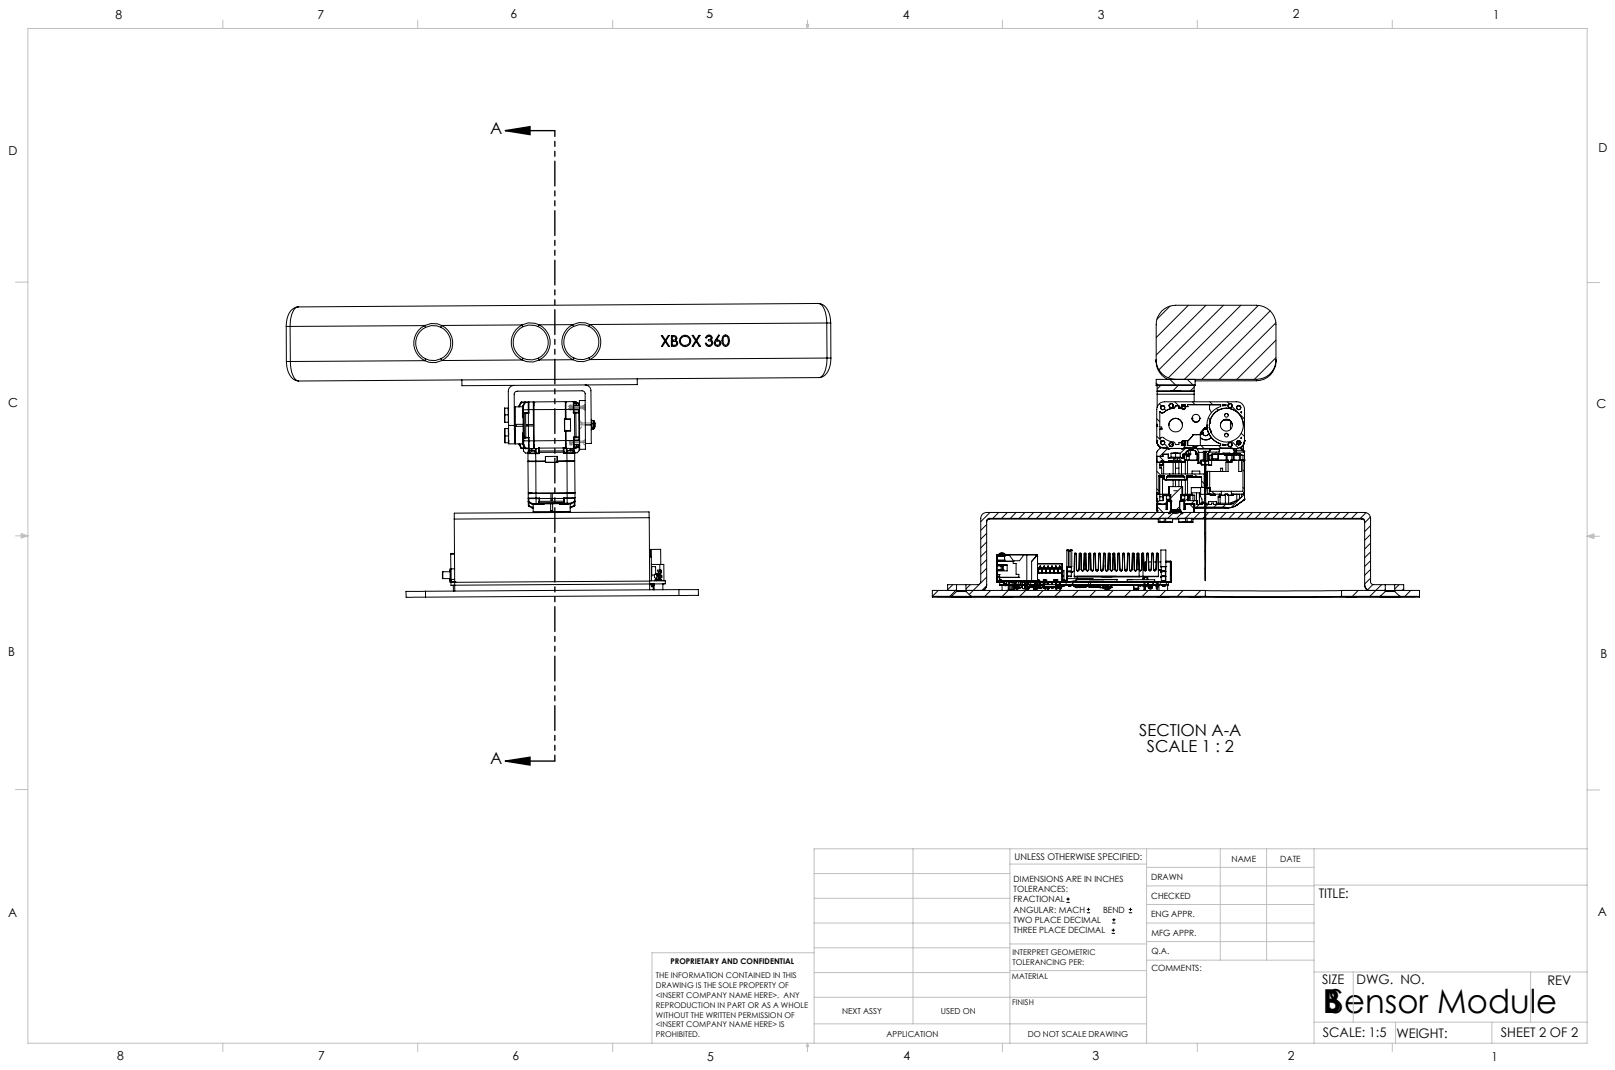
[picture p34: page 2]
SECTION A-A SCALE 1 : 2; NEXT ASSY; USED ON; ANGULAR: MACH; BEND; INTERPRET GEOMETRIC TOLERANCING PER:; ENG APPR.; MFG APPR.; DWG. NO.; REV; SCALE: 1:5 WEIGHT:; SHEET 2 OF 2; Sensor Module

UNLESS OTHERWISE SPECIFIED:

DIMENSIONS ARE IN INCHES
TOLERANCES:
FRACTIONAL
TWO PLACE DECIMAL
THREE PLACE DECIMAL

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

DO NOT SCALE DRAWING

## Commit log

2015-02-26 Added Semester 1 Files
    [(#112458) KSB1023A_T2X25NI.sldprt, (#129725) KSB1023A_M2_5X8Z.sldprt, (#31287) TOP_191.sldprt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]
2015-02-26 Added semester 2 files
    [16_pin_70mm_outer_diam_reference.SLDPRT, 16_pin_pogo_male_assembly.SLDASM, 16pin_PCB.SLDPRT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]
